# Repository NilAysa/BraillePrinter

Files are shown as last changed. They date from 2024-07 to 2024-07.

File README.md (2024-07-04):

# BraillePrinter
The Braille Printer is an embedded system designed to convert regular text into Braille on paper. It utilizes motorized axes and solenoids for precise dot placement, controlled by a Raspberry Pi computer. Ideal for accessibility, it enables the visually impaired to access printed text in Braille format.

Click to watch a video demonstration: https://www.youtube.com/watch?v=Feju8roK_-w

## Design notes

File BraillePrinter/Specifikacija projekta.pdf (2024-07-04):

### Specifikacija projekta: CNC mašina za ispis teksta u Braillovom pismu

Naziv projekta:

Braillovo pismo

Članovi tima:

- Irma Galijašević
- Ayša Nil
- Faruk Sijerčić

Opis projekta:
Cilj ovog projekta je dizajnirati i izraditi CNC mašinu koja će biti sposobna da koristi prikladnu iglicu za ispisivanje, odnosno istačkavanje riječi ili rečenica na Braillovom pismu. Mašina će biti izrađena kao funkcionalna maketa od šperploče i njen rad će biti kontrolisan razvijenom tehnikom koja radi u skladu sa proslijeđenim tekstom na latinici, koji se dalje ispisuje koristeći Braillova slova. Ovaj projekat je zamišljen kao pomoćno sredstvo za osobe sa oštećenim vidom, omogućavajući im da dobiju informacije preko Braillovog pisma na brz i efikasan način.

Funkcionalnosti:

1. Izrada makete od drveta: Mašina će biti napravljena od šperploče kako bi se postigla funkcionalnost i estetika.
2. Unos i prenos teksta: Korisnici će unositi riječi ili rečenice putem računara ili mobilnog uređaja, koje će se zatim prenijeti na CNC mašinu preko MQTT protokola.
3. Ispisivanje Braillovog pisma: Mašina će koristiti iglicu da ispiše uneseni tekst u Braillovom pismu na papir ili drugi prikladan materijal.
4. Kontrola kretanja: Step motori omogućavaju precizno kretanje po tri ose, omogućavajući tačan ispis Braillovih tačaka. Druga varijanta, umjesto kretanja po tri ose, je korištenje solenoida.

Ostale funkcionalnosti:

- Mogućnost podešavanja dubine istiskivanja tekstura.
- LCD displej za određeni korisnički interfejs i praćenje rada mačine

Hardverske komponente

- Raspberry Pi 3 B+
Centralna jedinica za kontrolu mašine i komunikaciju.
- Tri step motora
Omogućavaju precizno pomjeranje po X, Y i Z osi.
- Tri drajvera za motore
Upravljaju radom step motora, omogućavajući kontrolu pozicije i brzine.
- Drvena konstrukcija
Maketa CNC mašine bit će izrađena od drveta, pružajući stabilnost i potrebnu strukturu.
- Prikladna iglica za ispisivanje
Alat koji će se koristiti za bušenje tačaka na materijalu, formirajući Braillova slova.

Softverske komponente

- Kontrolni softver za Raspberry Pi
Omogućava komunikaciju između računara i CNC mašine. Interpretira ulazne podatke (tekst) i prevodi ih u odgovarajuće komande za step motore.
- MQTT protokol
Koristi se za prenos podataka sa računara na Raspberry Pi, omogućavajući bežičnu komunikaciju.

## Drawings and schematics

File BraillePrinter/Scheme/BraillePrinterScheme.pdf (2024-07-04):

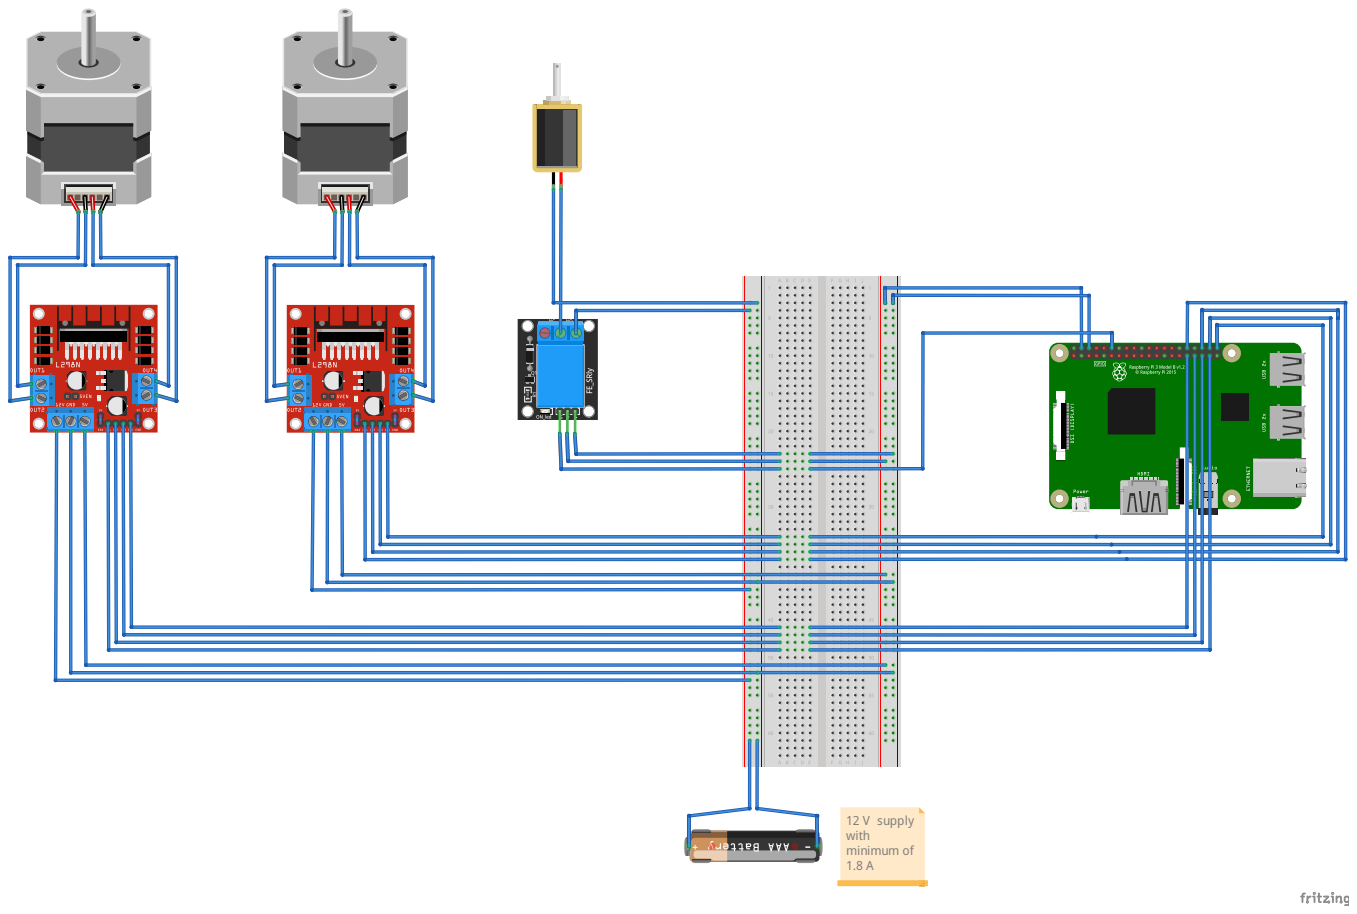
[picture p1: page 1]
12 V supply with minimum of 1.8 A

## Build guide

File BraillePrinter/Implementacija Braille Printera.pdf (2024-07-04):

# Implementacija Braille Printera

## 1. Uvod

Braille Printer predstavlja mašinu čija je namjena pretvaranje običnog teksta u Braille kucani tekst na papiru. Braille Printer je implementiran na način da koristi x i y osu kako bi mogao koordinirati položaj gdje će utisnuti tačku u papir.

Za ostvarivanje ovakve funkcionalnosti potrebni su sljedeći dijelovi:

- model,
- dva motora zajedno sa njihovim driverima,
- dvije navojne šipke,
- četiri metalne šipke,
- dva motor – navojna šipka priključka,
- relej,
- solenoid,
- izvor napajanja,
- računar (Raspberry Pi) sa periferijom.

## 2. Funkcionalnost fizičkog modela

Glavna ideja jeste da se mašina koordinira po osama te da utiskuje tačke. Problem fizičkog modela možemo razložiti na funkcionisanje osa i funkcionisanje solenoida.

## 2.1 Funkcionisanje osa

Da bi osa bila funkcionalna, potrebne su dvije metalne šipke kako bi se odredio smjer kretanja komponente (držač solenoida, držač papira) te navojna šipka koja je priključena na motor. Potrebno je ugraditi jednu maticu u komponente koje se kreću te kroz nju provući navojnu šipku. Kako se komponenta ne može okretati jer je usmjerena metalnim šipkama, ona će se kretati duž navojne šipke. Koliko distance će komponenta preći izravno zavisi od broja obrtaja koje motor uradi. Motoru se od strane računara šalju digitalni signali koji ga obrću. Na ovaj način, slanjem digitalnih signala sa računara, dobijamo kretanje komponente po jednoj osi.

## 2.2 Funkcionisanje solenoida

Kako bismo utiskivali tačkice u papir, potreban nam je solenoid. Solenoid ćemo koristiti preko releja. Ideja je da kada printer treba da utisne tačku, računar šalje signal releju da propusti struju kroz solenoid. Kada struja proteče kroz solenoid, igla udari u papir otiskujući rupu.

## 3. Funkcionalnost logičkog modela

Logički model možemo podijeliti na user interface, konverziju teksta u oblik podložan mašini za obrađivanje i komunikaciju sa fizičkim modelom.

## 3.1 User Interface

User interface predstavlja jednostavan prozorčić na računaru koji traži od korisnika da unese neki tekst te nakon njegovog unosa može kliknuti na dugme za printanje. Klikom na ovo dugme zamrzava se user interface jer je započelo procesiranje teksta te komunikacija sa fizičkim modelom. Nakon što se završi cijeli proces, korisnik može ponovo unijeti tekst.

## 3.2 Procesiranje teksta

Cilj procesiranja teksta je da se formatira tekst na način koji je kompatibilan sa specifičnim zahtjevima Braille štampača. Sastoji se od tri glavne funkcije: fillToBrailleFormat, parseText i toMachineBraille.

- Funkcija fillToBrailleFormat obrađuje ulazni tekst pretvarajući velika slova u mala i dodajući im donju crtu, te zamjenjujući cifre sa simbolom hash, čime se osigurava da tekst odgovara Brailleovim kodiranim konvencijama.
- Funkcija parseText zatim dijeli formatirani tekst na riječi i raspoređuje ih u linije određene dužine (lineLength), osiguravajući da svaka linija bude pravilno popunjena prazninama kako bi se održala konzistentna dužina.
- Funkcija toMachineBraille kombinuje ove korake tako što prvo konvertuje tekst pomoću fillToBrailleFormat, zatim ga organizuje u linije sa parseText i preokreće svaku liniju kako bi odgovarala orijentaciji kucanja štampača. Rezultat je lista formatiranih tekstualnih linija, spremnih za štampanje u Brailleovom pismu.

Konstante lineLength i numOfLines predstavljaju koliko Braille slova može stati u jednom redu te koliko redova jedna strana papira može imati.

## 3. Komunikacija sa fizičkim modelom

Za komunikaciju sa fizičkim modelom oformisane su klase Motor, Axis, Solenoid, koje se zajedno sa resursima (Matrice 2x3 za karaktere) koriste u glavnom programu. U glavnom programu se inicijalizira GUI za unos teksta, tekst se procesira prethodno razrađenim funkcijama te se onda šalje fizičkom modelu za štampanje.

## 3.1 Klasa Motor

Klasa Motor omogućuje kontrolu koraka motora potrebnog za pokretanje ose Braille printera. Glavne funkcionalnosti uključuju vođenje motora kroz određeni broj koraka (steps), koristeći unaprijed definiranu sekvencu koraka za rotaciju. Motor se okreće prema definiranim sekvencama i smjeru, što se kontrolira varijablom state. Prilikom destrukcije motora, pinovi se postavljaju na 0 radi sigurnosti..

## 3.2 Klasa Axis

Axis predstavlja klasu preko koje se pristupa motoru. Ona pokreće motor na rad, pamti koliko je koraka motor išao u nekom smjeru te pomoću ove informacije može da se vrati unazad tačno onoliko koraka kako bi motor se vratio na početnu poziciju odakle je krenuo.

## 3.3 Klasa Solenoid

Ova klasa koristi jednostavan princip korištenja solenoida preko releja. Releju se šalje signal da propusti struju kroz solenoid na određeno vrijeme.

## 3.4 Glavni program

Glavni program koordinira sve komponente sistema Braille Printera. Inicijalizira se GUI za unos teksta, tekst se zatim pretvara u Braille format te se provjerava njegova validnost za printanje. Prva petlja iterira kroz linije teksta, unutar nje druga petlja iterira kroz redove matrice slova, treća petlja kroz slova unutar linije teksta, dok se posljednja petlja izvrće unatrag kako bi ispravno orijentiralo kucanja teksta. Svaki slovo se pretražuje unutar matrice slova,provjerava se vrijednost na redu i i koloni j gdje je 1 predstavlja kucaj, a 0 nastavi dalje. Nakon svakog iskucanog reda linije teksta x osa se vraća na početnu poziciju, y osa prelazi u novi red za kucanje te se proces tako ponavlja. Nakon što se završi kucanje teksta obje komponente x i y ose se vraćaju na početni položaj

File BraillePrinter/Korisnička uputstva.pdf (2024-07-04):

# Korisnička uputstva

Korištenje ove aplikacije je izuzetno jednostavna. Sve što je potrebno jeste da se klikne na BraillePrinter.desktop. Ovo će da pokrene skriptu glavnog programa. Korisniku će zatim biti prikazan grafički interfejs u kojem se traži unos teksta. Nakon što se postavi i fiksira papir na printeru i unese željeni tekst, korisnik treba pritisnuti dugme za printanje te će Braille Printer da izvršava svoju funkciju. Nakon što printer obavi svoj rad, od korisnika se ponovo traži unos teksta.

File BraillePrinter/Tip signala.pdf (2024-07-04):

# Tip signala

Motor | Digitalni signali // Motoru se preko drajvera šalju digitalni signali o načinu propuštanja struje u svrhu obrtanja istog
Relej | Digitalni signali // Releju se šalju digitalni signali u svrhu propuštanja struje kroz solenoid

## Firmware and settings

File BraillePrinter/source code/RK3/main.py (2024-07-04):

#!/usr/bin/python3

import RPi.GPIO as GPIO
from axis import *
from solenoid import *
from text_processing import *
from gui import BraillePrinterGUI
from resources import BrailleAlphabet
import time
GPIO.setmode(GPIO.BCM)
GPIO.setwarnings(False)


def printBraille(text):
    try:
        text = toMachineBraille(text)
    
        if len(text) > numOfLines:
            print("Text is too long")
            return

        for line in text:
            for i in [0, 1, 2]:
                for letter in line:
                    for j in [1, 0]:
                        if BrailleAlphabet[letter][i][j]:
                            z.push()
                            z.push()
                            print(".", end = "")
                        else:
                            print(" ", end = "")
                        time.sleep(.5)
                        x.goForward(181) #2.5mm
                    print("|", end = "")
                    x.goForward(50) #1.0mm
                print("")
                x.startPosition()
                y.goForward(400) #2.5mm
            print("")
            y.goForward(800) #5mm
        y.startPosition()
    except KeyboardInterrupt:
        x.startPosition()
        y.startPosition()

x = Axis(6,13,19,26)
y = Axis(12,16,20,21)
z = Solenoid(18) 
BraillePrinterGUI(printBraille)

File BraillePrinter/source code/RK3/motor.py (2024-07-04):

import RPi.GPIO as GPIO
import time


class Motor:
    sequence = [
        [1, 0, 1, 0],
        [0, 1, 1, 0],
        [0, 1, 0, 1],
        [1, 0, 0, 1]
    ]
    
    def __init__(self, pinA, pinB, pinC, pinD):
        self.pins = [pinA, pinB, pinC, pinD]
        self.direction = 1
        self.state = 0
        
        for pin in self.pins:
            GPIO.setup(pin, GPIO.OUT)
            GPIO.output(pin, 0)
     

    def setDirection(self, d):
        self.direction = 1 if d > 0 else -1


    def run(self, steps):
        for _ in range(steps):

            self.state += self.direction

            if self.state == -1:
                self.state = 3
            elif self.state == 4:
                self.state = 0
    
            GPIO.output(self.pins, self.sequence[self.state])
            time.sleep(0.0032)
            
        GPIO.output(self.pins, [0, 0, 0, 0])
            

    def __del__(self):
        for pin in self.pins:
            GPIO.output(pin, 0)
